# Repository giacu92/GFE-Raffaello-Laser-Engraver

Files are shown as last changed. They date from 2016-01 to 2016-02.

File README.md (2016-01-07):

# GFE-Raffaello-Laser-Engraver
This repo contains all the files of my Arduino Nano based Laser Engraver firmware for Arduino.

* Author: Giacomo Mammarella
* email: giacomo.mammarella@student.univaq.it

# File list:
* [grbl09j_GFE.hex](https://github.com/giacu92/GFE-Raffaello-Laser-Engraver/blob/master/grbl09j_GFE.hex): is the hex file precompiled for my Arduino Nano controller Board.
* [Laser engraver V2.sch](https://github.com/giacu92/GFE-Raffaello-Laser-Engraver/blob/master/Laser%20engraver%20V2.sch): the Cadsoft Eagle 6.5 schematic file for the board.
* [Laser engraver V2.brd](https://github.com/giacu92/GFE-Raffaello-Laser-Engraver/blob/master/Laser%20engraver%20V2.brd): the Cadsoft Eagle 6.5 board file.
* Nano grbl.png: useful as connections reference guide.

# .hex file characteristics: grbl09j_GFE.hex 
* Changed defaults for the GFE Raffaello Laser Engraver to match motor and machine parameters.
* Changed homing cycle: $H now ignores the z-axis and perform homing cycle for 2 axis machines.
* Mapped PWM Spindle control (pin: D11) on the range from 0 (1/255, Laser still ON!) to 12.000 (DC). The value 12.000 was chosen to match bCNC parameter for spindle max speed. 

# Realize the board, BOM:
To realize the board you'll need the following parts. And the links to buy 'em:
* [Arduino Nano Compatible board](http://www.banggood.com/ATmega328P-Arduino-Compatible-Nano-V3-Improved-Version-With-USB-Cable-p-933647.html) from Banggood.com
* [Mini DC-DC Converter](http://www.banggood.com/Mini-DC-DC-Converter-Step-Down-Module-Adjustable-Power-Supply-p-920327.html) from Banggood.com
* 2 x [A4988 Stepper Driver](http://www.banggood.com/5Pcs-3D-Printer-A4988-Reprap-Stepper-Motor-Driver-Module-p-952527.html) i got mine from Banggood.com too, bought in pack of 5 for about $8,00.
* 2 x [3 poles DIP Switches](http://www.aliexpress.com/item/DIP-switch-3-way-2-54mm-DIP-Switches-3P/939142709.html) from Aliexpress.com
* 1 x [2.1mm DC Jack Female Plug Connector](http://www.aliexpress.com/item/DC-Power-adapter-dc-jack-connector-DC005-5-5-X-2-1-mm-50-pcs-lot/32352870494.html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,searchweb201644_2_10001_10002_10005_10006_10003_10004_62,searchweb201560_6,searchweb1451318400_6149), but I got mine from a local Hardware Store
* 2 x 100uF/25V Electrolitic Capacitor from Hardware Store
* 3mm red led, 1N4001 diode and a 4,7k resistor for the led.

# Connections:
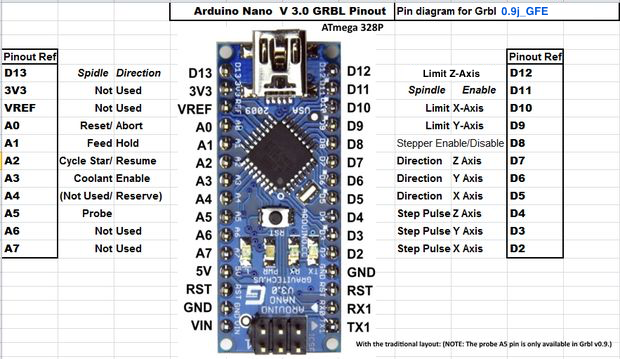
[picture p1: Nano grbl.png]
Arduino Nano

Board

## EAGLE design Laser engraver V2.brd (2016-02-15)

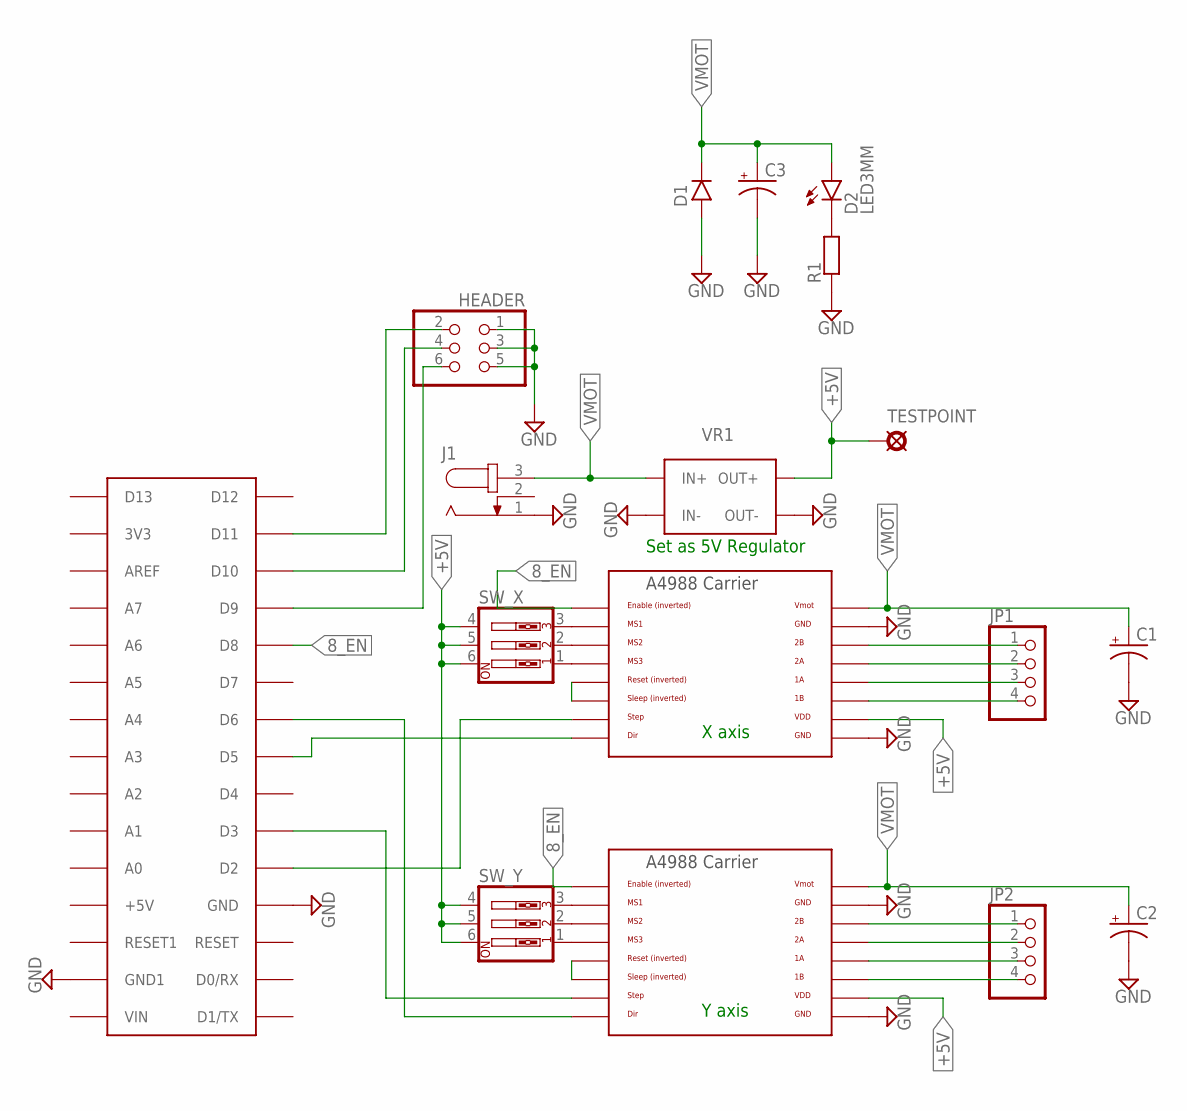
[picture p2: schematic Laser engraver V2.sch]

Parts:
C1, C2: 0501; 050_020_1
C3: 0631; 063_025
D1: 1N400X.3; DO41-3
D2: LED3MM
HEADER: PINHD-2X3; 2X03
J1: JACK-PLUG0; SPC4077
JP1, JP2: PINHD-1X4; 1X04
MOTOR_X: A4988BREAKOUT
MOTOR_Y: A4988BREAKOUT
R1: 6MM-EU; R0207/3
SW_X: SW_DIP-3; EDG-03
SW_Y: SW_DIP-3; EDG-03
TESTPOINT: PAD; SQUARE
U$3: ARDUINONANO; PDIP-32
VR1: VOLTAGE_REG_BANGGOOD; VOLTAGE_REG

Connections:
8_EN: MOTOR_X.EN, MOTOR_Y.EN, U$3.D8
+5V: MOTOR_X.VDD, MOTOR_Y.VDD, SW_X.4, SW_X.5, SW_X.6, SW_Y.4, SW_Y.5, SW_Y.6, TESTPOINT.1, VR1.O+1 (OUT+), VR1.O+2 (OUT+)
GND: C1.-, C2.-, C3.-, D1.A, HEADER.1, HEADER.3, HEADER.5, J1.1, MOTOR_X.GND, MOTOR_X.GND@0 (GND), MOTOR_Y.GND, MOTOR_Y.GND@0 (GND), R1.1, U$3.GND, U$3.GND1, VR1.IN-1 (IN-), VR1.IN-2 (IN-), VR1.O-1 (OUT-), VR1.O-2 (OUT-)
unnamed: MOTOR_X.MS3, SW_X.1
unnamed: MOTOR_X.MS2, SW_X.2
unnamed: MOTOR_X.MS1, SW_X.3
unnamed: MOTOR_Y.MS3, SW_Y.1
unnamed: MOTOR_Y.MS2, SW_Y.2
unnamed: MOTOR_Y.MS1, SW_Y.3
unnamed: HEADER.6, U$3.D9
unnamed: MOTOR_X.DIR, U$3.D5
unnamed: MOTOR_X.STEP, U$3.D2
unnamed: MOTOR_Y.DIR, U$3.D6
unnamed: MOTOR_Y.STEP, U$3.D3
unnamed: MOTOR_Y.RST, MOTOR_Y.SLP (SLEEP)
unnamed: MOTOR_X.RST, MOTOR_X.SLP (SLEEP)
unnamed: HEADER.4, U$3.D10
unnamed: HEADER.2, U$3.D11
unnamed: JP1.1, MOTOR_X.2B
unnamed: D2.K (C), R1.2
unnamed: JP1.4, MOTOR_X.1B
unnamed: JP1.3, MOTOR_X.1A
unnamed: JP1.2, MOTOR_X.2A
unnamed: JP2.1, MOTOR_Y.2B
unnamed: JP2.2, MOTOR_Y.2A
unnamed: JP2.3, MOTOR_Y.1A
unnamed: JP2.4, MOTOR_Y.1B
VMOT: C1.+, C2.+, C3.+, D1.C, D2.A, J1.3, MOTOR_X.VMOT, MOTOR_Y.VMOT, VR1.IN+1 (IN+), VR1.IN+2 (IN+)

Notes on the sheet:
X axis
Y axis
Set as 5V Regulator

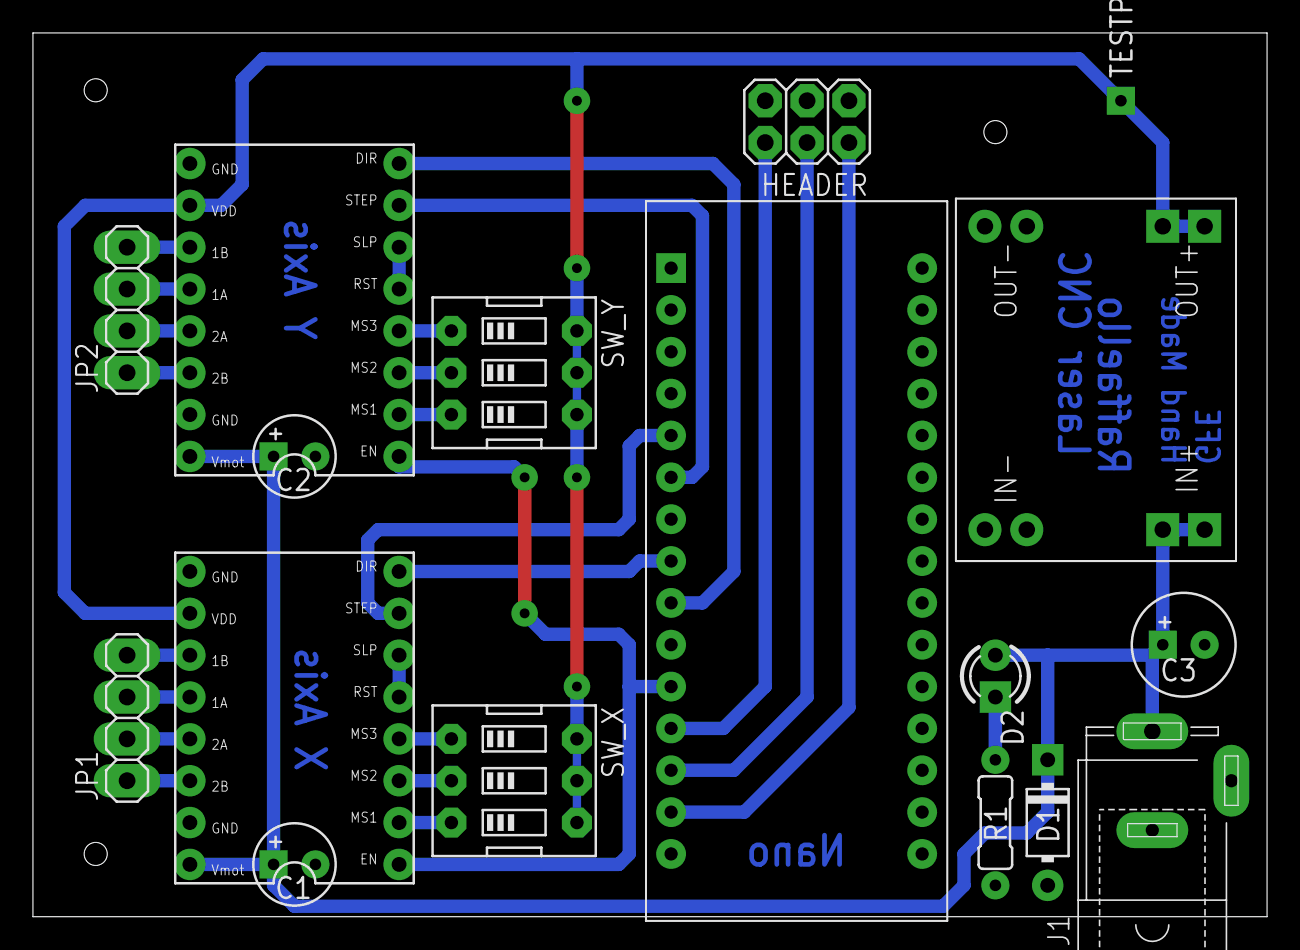
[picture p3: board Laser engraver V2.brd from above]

Board: 2 copper layers, 74.9 x 53.6 mm, 17 parts (0 on the bottom side), 28 nets.

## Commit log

2016-01-07 grbl based hex file of my Raffaello Laser Engraver. It has the following options: Homing ignores the Z-axis Spindle PWM set as 100% when at 12000rpm on bCNC
2016-01-07 eagle files
    [Laser engraver V2.brd, Laser engraver V2.sch]
2016-01-07 Eagle 6.5 schematic file
    [Laser engraver V2.sch]
2016-01-07 Eagle 6.5 board file
    [Laser engraver V2.brd]
2016-01-07 Arduino Nano configuration of 0.9j_GFE.hex firmware
2016-01-07 Hex file for grbl 0.9j_GFE. Added default_GFE.h eeprom settings
